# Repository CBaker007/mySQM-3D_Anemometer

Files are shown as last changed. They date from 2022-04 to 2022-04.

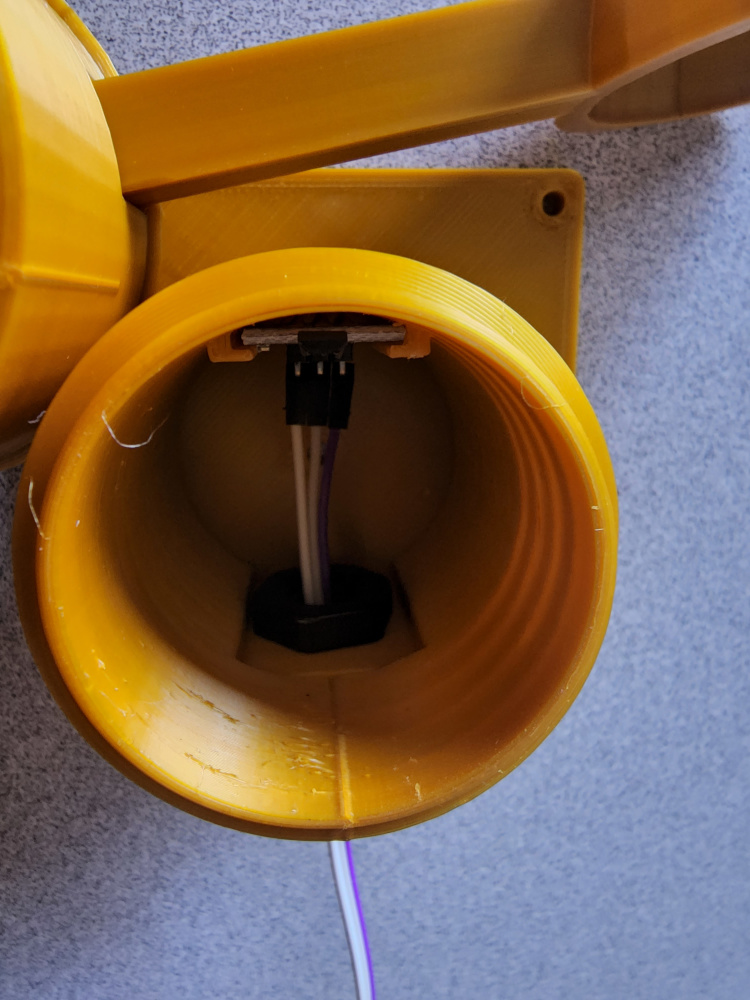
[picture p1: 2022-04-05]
Pictures/20220405_112956.jpg

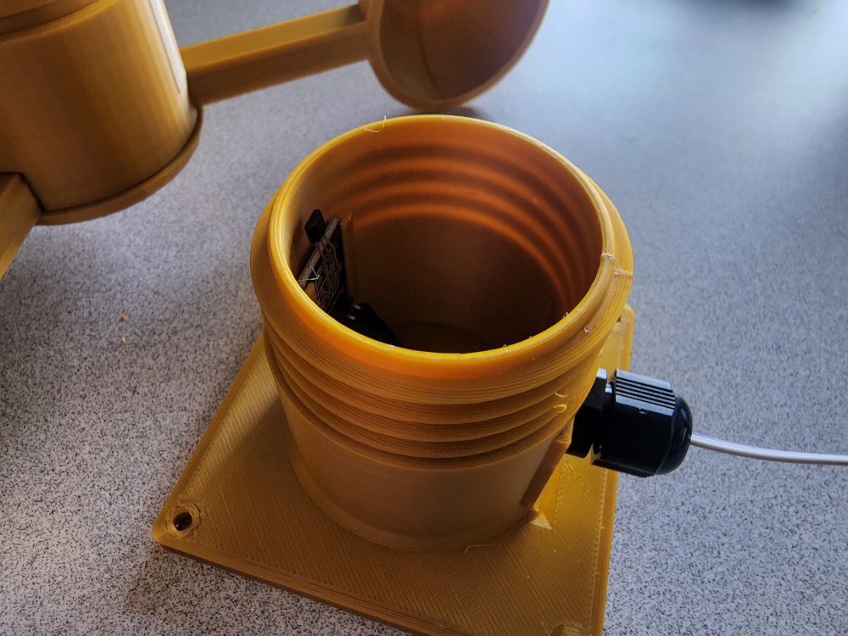
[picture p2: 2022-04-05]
Pictures/20220405_113105.jpg

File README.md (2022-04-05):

# mySQM-3D_Anemometer

FROM: https://github.com/CBaker007/mySQM-3D_Anemometer/

BY: Christopher Baker (CBaker007 on GitHub)

LICENSE: Creative Commons - Attribution-NonCommercial-ShareAlike (BY-NC-SA)

WHAT: A 3D printed Anemometer based on the design from mySQM+ DIY SQM Weather Station on Sourceforge.

ATTRIBUTE:  This is a re-work of the design by Robert Brown found on SourceForge:
            https://sourceforge.net/projects/mysqmproesp32/files/Wind%20Speed%20Sensor%20Anemometer/mySQMPROESP-3DPRINTER/

These 3D printed parts are released into the public domain and also follow the copyright indicated in the 
mySQM+ DIY Weather Station found on Sourceforge:
    "COPYRIGHT RESTRICTIONS
    The schematic, firmware and other code and ideas are released into the public domain. Users are free to
    implement these for their personal use, but may NOT sell projects based on (or derived from) this project
    for commercial gain.
    1. You cannot sell kitsets or assembled units to others
    2. You cannot copy the design and code and make your own version to sell to others, even if you make 
       some code changes or change pin designations
    3. You cannot use these designs and code ideas to make your own controller and sell versions of those 
       to others"

Due to non-commercial use, this isn't really public domain or CC0.  Therefore, I believe the correct 
Creative Commons license, and what I am using for this repository, is 
"Attribution-NonCommercial-ShareAlike", aka BY-NC-SA. (More info: https://creativecommons.org/)

Coding for the Anemometer will be based on my code integrated into my existing DIY Weather Station, which will 
be made available on my GitHub in the near future when integration is complete.  Should work fine with the 
mySQM+ DIY SQM Weather Station code too as all critical dimensions remained the same on my re-work.

Main Reasons for Re-Work:
A. Don't like using glue on PETG parts.   Not reliable from my experience.  All parts screw together 
   with internal threads or screws.
B. Wanted to be able to take it apart for repair or updates.   Original relies on press fit for bearing 
   and made assembly/disassembly difficult.
C. Wanted to make the rotating assembly fixed vertically so it could not move up/down.

NOTES:
* Followed original instructions and non-3D parts list as a guide.
* All the original parts should fit and work, minus possibly the Hall Effect Sensor may not mount
  in the slot in my design (taller/wider??). You would have to mount it as done in the original design.
* Purchased all parts in US from Amazon with the following specifications/notes/links:
  - Bearing:  The key specification is this is a 6004 bearing which is a common size.  I purchased 
    a 2RS model (rubber seal on top and bottom) as specified in the orginal guide but did not like
    the friction it created.  While not as good of seal to keep water and dirt out, I ended up
    buying a ZZ model (steel seal on top and bottom).  Much less friction.
    PGN - 6004-ZZ Shielded Ball Bearing - C3-20x42x12 - Lubricated - Chrome Steel
    https://www.amazon.com/gp/product/B07GWZ48SK/
  - Hall Effect Magnetic Sensor: I could not find the "Keyes-024" model on Amazon though there
    are many other brands.  The originally spec'd model offers a digital and analog signal
    output and runs on 3.3V.  The one I purchased only has the required digital output
    and runs on 3.3V or 5.0V. My design has a holder for this sensor.
    There are many other models on Amazon.
    HiLetgo Hall Effect Magnetic Sensor Module 3144E A3144
    https://www.amazon.com/gp/product/B01NBE2XIR/
  - Cable Gland:  I did not use a pre-wired bulkhead connnector.  Instead I used a waterproof
    cable gland size PG7 and some tape. I already have a set of assorted sizes.  Many PG7 
    cable glands are available on Amazon, but here is one example (make sure you get size PG7), 
    looks like the threads are long enough (4 mm needed as I recall, check STL):
    BouPower 20Pcs Nylon Cable Gland Waterproof IP68 Adjustable Cable Connectors Joints with Gaskets
    https://www.amazon.com/BouPower-Waterproof-Adjustable-Connectors-Gaskets/dp/B08QZ97C5B/
  - Magnets:  I already had a supply of magnets but they are readily available on Amazon.
    Personally I like the assortment packs which are more, but I use them for other projects.
    One example of a small pack of 6x3mm magnets on Amazon:
    TRYMAG Refrigerator Magnets 45 Pcs, Small Round Disc Fridge Magnets
    https://www.amazon.com/TRYMAG-Refrigerator-Multi-Use-Cylinder-Whiteboard/dp/B09MRMXMCW
 
 3D Printing NOTES
 *  All Items printed with 5 walls, at 30% infill, using PETG.
 *  Supports:
    - "Base - Top" enabled for threads only, removed for outside overhangs.
      Printed with threads on top.
    - "Base - Bottom" enabled with supports removed for the outside overhang and 
      inside sensor holder.  Be sure to flip so square base is down.
    - "Hub - Arms" printed with cup opening facing down with supports.
    - "Hub - Main" printed with supports and arm openenings down.
    - "Hub - Top" and all "Hub - Spacers" printed without supports and widest part down.
 *  "Hub - Spacer 1" goes in Hub at the top before the bearing.
 *  "Hub - Spacer 2" goes in hub after the bearing, before the magnet holder (LeverArm).
 *  "Hub - Spacer 3" goes between the screw threads of the "Base - Top" and "Base - Bottom"
    with the wider part facing the "Base - Bottom".  Locks the bearing in place when
    top and bottom tightened together.
 *  The "LeverArmFinal" is taken from the original design.

CAD Files (Again, shared as attribute required, non-commercial, share-alike.)
 *  The Base (top and bottom) were done in Fusion 360 and the .f3d files are available
    on this GitHub reposoitory if you wish to re-work things for your use.  
    The .STL files for printing are already on respository.
 *  The remaining files were developed in TinkerCAD.  You must create a free account
    if you want to rework them there.  (They don't allow any CAD export and the
    transfer to Fusion 360 isn't working for me.)  The .STL files for printing are
    in this respository.

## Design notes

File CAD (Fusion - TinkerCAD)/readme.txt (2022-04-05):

////////////////////
//// CAD Files /////
////////////////////

FROM: https://github.com/CBaker007/mySQM-3D_Anemometer/
BY: Christopher Baker (CBaker007 on GitHub)
LICENSE: Creative Commons - Attribution-NonCommercial-ShareAlike (BY-NC-SA)

Original Release
=================
  Fusion 360 Export
  *  Base - Btm (v7).f3d
  *  Base - Top (v7).f3d
  
  TinkerCAD
  *  Online, create free account
  *  Find in collection:
     Anemometer (partial)
     https://www.tinkercad.com/dashboard?type=tinkercad&collection=projects&id=6WtAah7DIMl

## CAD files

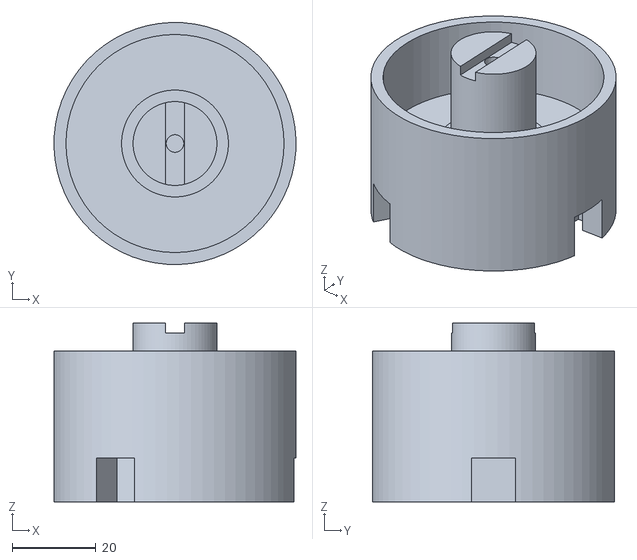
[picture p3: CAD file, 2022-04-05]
3D Printer Files (STL)/Anemometer - Hub - Main (v1).stl
57.7 x 57.7 x 42.6

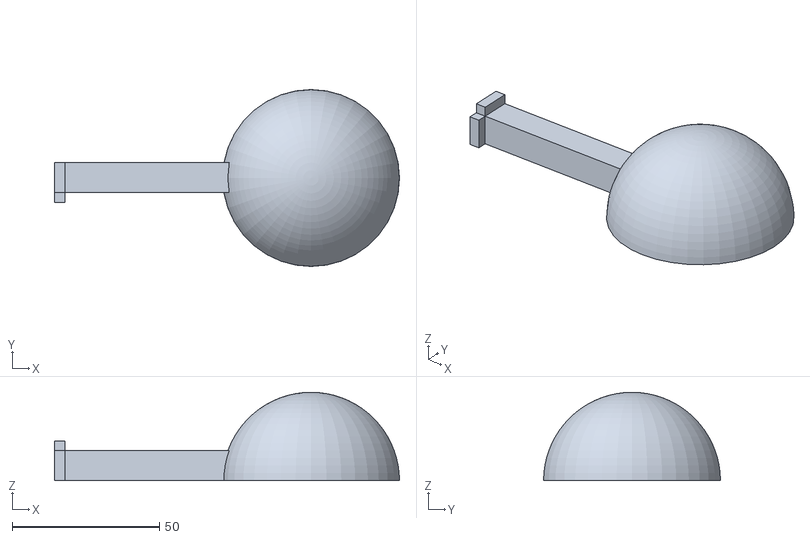
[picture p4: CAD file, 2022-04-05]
3D Printer Files (STL)/Anemometer - Hub - Arm (v3).stl
117.0 x 60.0 x 30.0

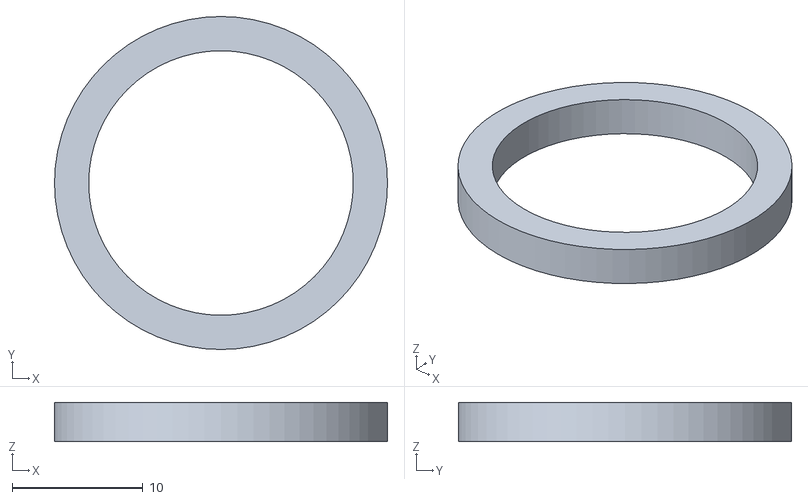
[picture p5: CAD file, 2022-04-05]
3D Printer Files (STL)/Anemometer - Hub - Spacer 1 (v1).stl
25.5 x 25.5 x 3.00

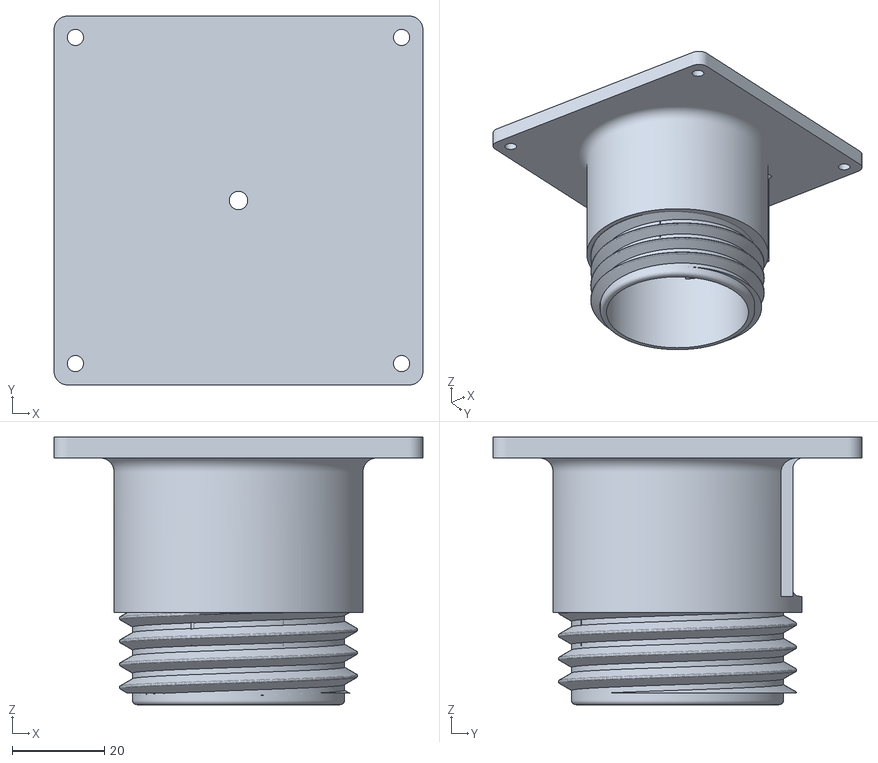
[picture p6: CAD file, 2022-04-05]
3D Printer Files (STL)/Anemometer - Base - Btm (v7).stl
80.0 x 80.0 x 58.0

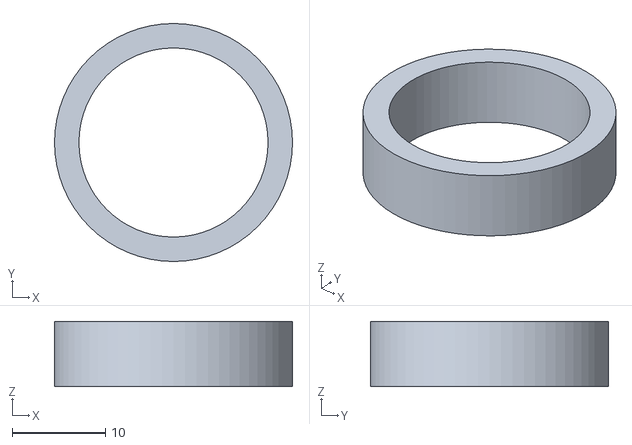
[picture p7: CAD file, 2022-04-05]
3D Printer Files (STL)/Anemometer - Hub - Spacer 2 (v1).stl
25.5 x 25.5 x 7.00

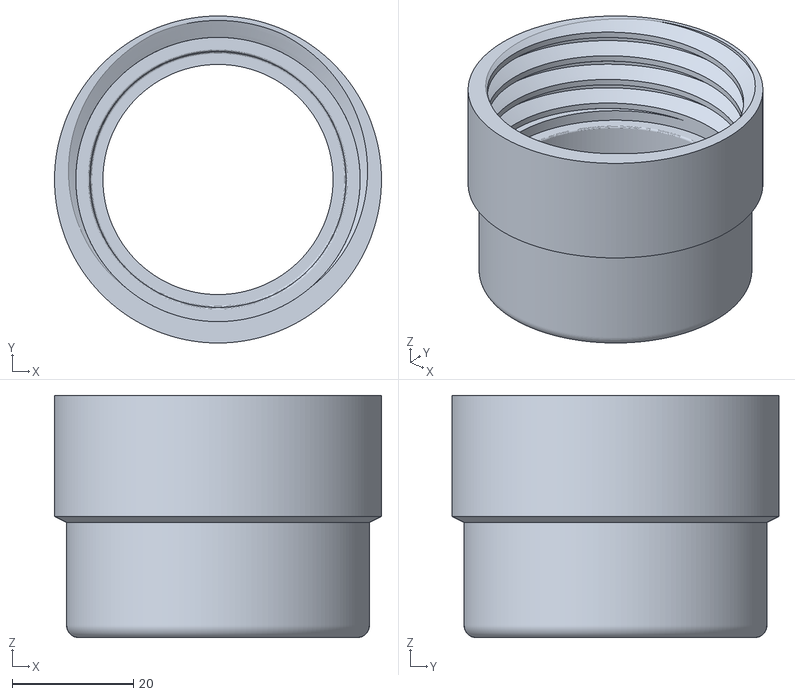
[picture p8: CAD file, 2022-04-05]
3D Printer Files (STL)/Anemometer - Base - Top (v7).stl
54.0 x 54.0 x 40.0

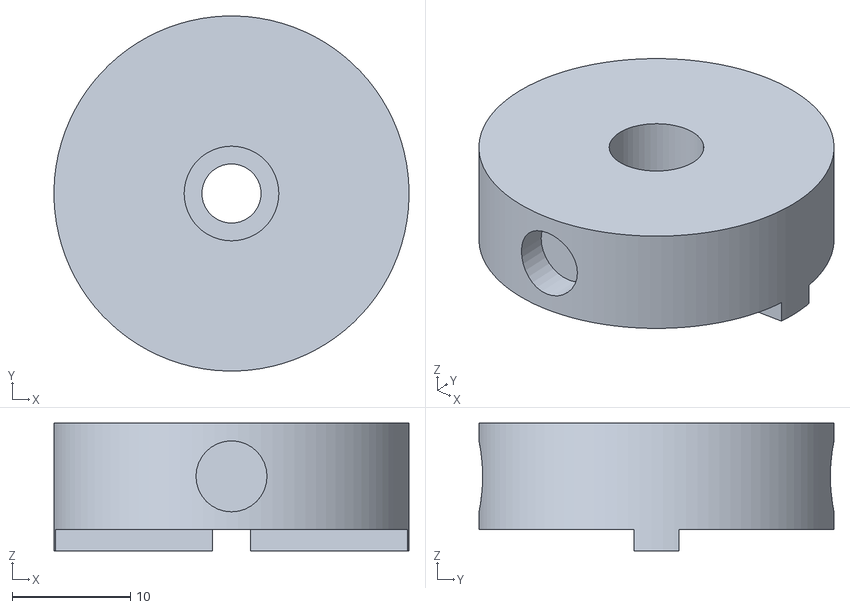
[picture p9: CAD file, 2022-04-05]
3D Printer Files (STL)/Anemometer - Hub - LeverArmFinal (Orig).stl
30.0 x 30.0 x 10.8

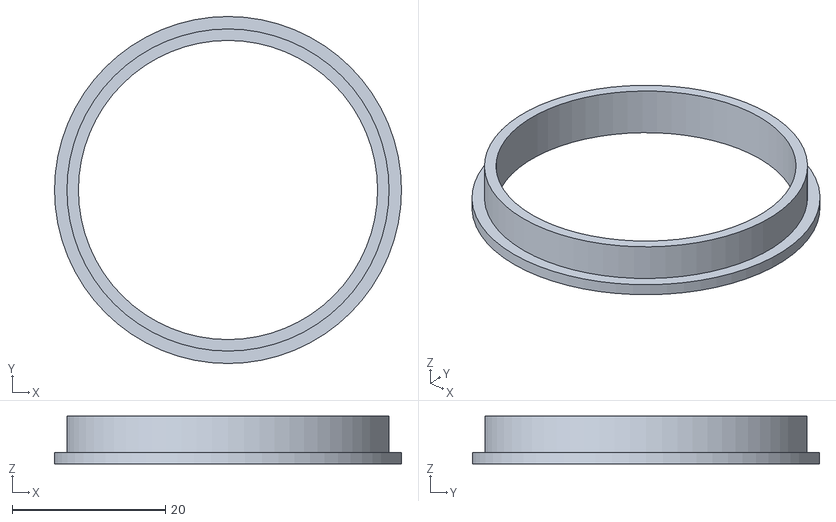
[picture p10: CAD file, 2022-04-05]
3D Printer Files (STL)/Anemometer - Hub - Spacer 3 (v1).stl
45.2 x 45.2 x 6.25

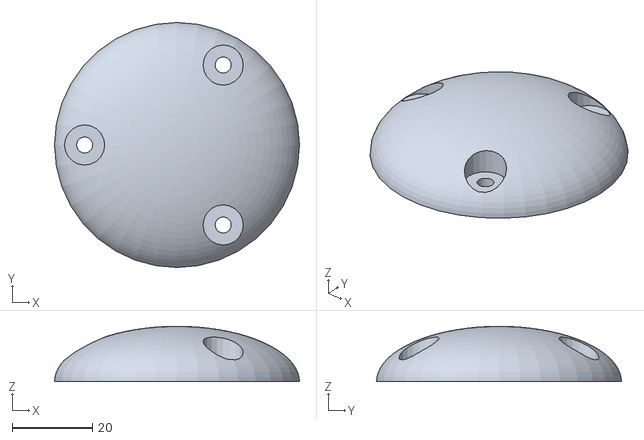
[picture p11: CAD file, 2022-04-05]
3D Printer Files (STL)/Anemometer - Hub - Top (v1).stl
61.0 x 61.0 x 13.8

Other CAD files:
CAD (Fusion - TinkerCAD)/Base - Btm (v7).f3d
CAD (Fusion - TinkerCAD)/Base - Top (v7).f3d

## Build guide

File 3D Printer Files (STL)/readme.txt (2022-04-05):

////////////////////////////////
//// 3D Printer Files (STL) ////
////////////////////////////////

FROM: https://github.com/CBaker007/mySQM-3D_Anemometer/
BY: Christopher Baker (CBaker007 on GitHub)
LICENSE: Creative Commons - Attribution-NonCommercial-ShareAlike (BY-NC-SA)

Original Release
=================
- Anemometer - Base - Btm (v7)
- Anemometer - Base - Top (v7)
- Anemometer - Hub - Arm (v3)
- Anemometer - Hub - Main (v1)
- Anemometer - Hub - Spacer 1 (v1)
- Anemometer - Hub - Spacer 2 (v1)
- Anemometer - Hub - Spacer 3 (v1)
- Anemometer - Hub - Top (v1)
- Anemometer - Hub - LeverArmFinal [From Original]
